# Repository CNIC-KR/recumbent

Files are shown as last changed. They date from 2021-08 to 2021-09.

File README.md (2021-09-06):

# 방치자전거 부품으로 3륜 리컴번트 만들기

YouTube 비디오 링크:  

IMAGE ALT TEXT HERE (https://www.youtube.com/watch?v=EfHd-qzypDQ)

___
본 자전거는 미국 DIY 창작자 Atomic Zombie 의 Streetfox Tadpole Trike 설계를 기반으로 제작되었습니다.  
제작 도면은 Atomic Zombie의 웹사이트에서 직접 구입하셔야 합니다.  
[https://www.atomiczombie.com/streetfox-tadpole-trike-diy-plan/](https://www.atomiczombie.com/streetfox-tadpole-trike-diy-plan/)  
___
**주의**

충남사회혁신센터는 공유된 리컴번트 자전거 설계의 안전성, 신뢰성, 내구성, 기능을 보장하지 않습니다. 또한 공유된 자전거 설계를 통해 제작된 어떠한 장치의 안성,신뢰성, 내구성, 기능에 대해서도 책임을 지지 않습니다. 공유된 설계에 기반해 장치를 제작하는 것은 전적으로 제작자의 재량에 의한 것이며 충남사회혁신센터는 공유된 정보를 활용해 내려진 결정이나 행동에 대해서 법적인 책임이 없습니다. 

**안전** 

본 제작 가이드에서 사용하는 공구들은 적절한 안전장비를 갖추지 않고 작업할 경우 제작자에게 상해를 입힐 수 있습니다. 특히 용접의 경우 전문적인 교육을 이수하는 것이 안전한 작업을 위해 바람직합니다. 작업시 보안경, 용접장갑, 용접마스크, 귀마개 등을 갖추고 안전하게 작업하세요! 
___

**•0_리컴번트 제작 가이드:**  
제작을 진행하신 김성수님의 제작 팁이 적혀있는 한국어 가이드입니다.  
https://forms.gle/e7z2dzJB1erC4kB48 에서 면책특약에 동의하신 후 다운받으실 수 있습니다.  
도면과 실제 제작이 다른 부분이 있으시 재료 구입전 **꼭** 읽어보셔야 합니다. 

**•1_리컴번트 부품 목록:**  
제작에 필요한 재료들의 수량과 구입처가 적혀있습니다.  

**•2_용접지그 도면:**  
프레임 용접에 필요한 용접지그의 2D 도면입니다.  
구조를 파악하기 위한 3D 파일은 아래 링크에서 확인하실 수 있습니다.  

**•용접지그 3D 파일:**  
https://cad.onshape.com/documents/e19db32aaa2f906931428a36/w/65d13d293f960f246c17134b/e/6adec4346e6a5c44e0e556bb

**•3_헤드튜브 바이스 도면/4_헤트튜브 바이스 하부 도면:**  
지그에서 헤드튜브 고정에 사용되는 바이스 상•하부의 도면입니다. 각파이프를 가공하여 제작합니다.  

**•5_tube_notcher_AngleCalculation.f3d :**  
헤드 튜브와 암 프레임이 만나는 각도를 표시한 선으로만 이루어진 CAD 도면입니다. 제작가이드 4.리컴번트 제작 부분을 참고하세요.  
 f3d 확장자는 Autodesk Fusion 360으로 열람하셔야합니다.  
 DWG파일과 캡쳐이미지를 첨부하였습니다.  

**•6_tube_notcher_spacer.f3d:**  
원형파이프 노칭기에 40mm x 40mm사각파이프를 물려서 가공할 수 있는 어답터입니다. 3D 프린트하여 사용하셔야 합니다. STL 파일과 캡쳐이미지를 첨부했습니다.

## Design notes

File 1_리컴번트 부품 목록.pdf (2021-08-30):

지그용 부품 | 항목 | 규격 | 갯수
알루미늄 프로파일 40x80mm | 600mm | 2 | http://www.profileok.com/shop/item.php?it_id=1400000012
알루미늄 프로파일 40x80mm | 1000mm | 1
알루미늄 프로파일 40x80mm | 920mm | 1
알루미늄 프로파일 40x80mm | 350mm | 2 본 부재의 길이를 늘려서 서서 작업 할 수 있도록 할 수 있다.
알루미늄 프로파일 40x80mm | 780mm | 1 납품한 지그와 다른 부분으로써 바퀴를 끼웠을때 걸리는 것을 피하고자 팔의 길이를 줄였다.
알루미늄 프로파일 40x80mm | 300mm | 2
알루미늄 프로파일 40x80mm | 200mm | 2
80면용 앵글 | 75x75 | 8 | http://www.profileok.com/shop/item.php?it_id=1500000008
40면용 앵글 | 80x37 | 6 | http://www.profileok.com/shop/item.php?it_id=1500000006
80면용 앵글 | 75x40 | 1 | http://www.profileok.com/shop/item.php?it_id=1500000004
샘스렌치볼트 | M8 25 | 100
스프링 너트 | M8 | 100
조절좌 | A-VP 12-90 | 4 | http://www.profileok.com/shop/item.php?it_id=1700000002
풋베이스 | DAFB4080(M12) | 4 조절좌를 달기 위한 판 | http://www.profileok.com/shop/item.php?it_id=1500000051
M8x25 렌치볼트 | 16 풋베이스를 프로파일에 연결하기 위한 볼트
플라스틱 앤드캡 | DEC4080 | 10 | http://www.profileok.com/shop/item.php?it_id=1500000039
클램프 레버 | M8x30 | 4 | https://www.coupang.com/vp/products/1504455925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
클램프 레버 | M8x50 | 2 | https://www.coupang.com/vp/products/1504455925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
노브 | M8x50 | 4 | https://www.coupang.com/vp/products/1495893683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
볼반 바이스 | 2 | https://www.coupang.com/vp/products/2053120294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
m10 와샤 | 20
튜브 노칭기 | 파이프노칭기 파이프홀가공 PNM1-1.2 PIPE | 1 | https://www.coupang.com/vp/products/191613037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
모터 | 바팡 750w 키트 | 바이크샵에게만 판매하기 때문에 전화해서 사장님께 허락을 받아야 한다. | https://bafangs.com/?page_id=68
스피드 센서 케이블 연장선 | 1 | https://www.aliexpress.com/item/32985406351.html?spm=a2g0s.9042311.0.0.44024c4dlOSSRs
쓰로틀 케이블 연장선 | 1 | https://www.aliexpress.com/item/1005001593406432.html?spm=a2g0s.9042311.0.0.44024c4dlOSSRs
xt60 커넥터 | 암수 | 2 | https://www.coupang.com/vp/products/5579805640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
실리콘 피복케이블 _레드 | AWG 16 | 2m | https://www.coupang.com/vp/products/4938811079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
실리콘 피복케이블 _블랙 | AWG 16 | 2m | https://www.coupang.com/vp/products/4938811079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
브레이크 | 브레이크 레버 | 앞바퀴용 더블 케이블 레버 | 납품한 자전거에는 설치 되어 있지 않음, 구매한 것이 나중에 배송왔으나 엉뚱한 트리플케이블용이https://www.aliexpress.com/item/4000481092339.html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
디스크 브레이크 | 드럼 브레이크를 쓰는 자전거를 부품으로 쓸 때 교체 가능 | https://www.aliexpress.com/item/33003381582.html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
디스크 브레이크 캘리퍼 브라켓 | 드럼 브레이크를 쓰는 자전거를 부품으로 쓸 때 교체 가능 | https://www.aliexpress.com/item/1005001273485667.html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
디스크 브레이크 캘리퍼 브라켓 | 새로 찾은 것 _ 드럼 브레이크를 쓰는 자전거를 부품으로 쓸 때 교체 가능 | https://www.aliexpress.com/item/1005002362649962.html?spm=a2g0s.8937460.0.0.478f2e0ea6u5FI
디스크 브레이크 디스크 어댑터 | 드럼 브레이크를 쓰는 자전거를 부품으로 쓸 때 교체 가능 | https://www.aliexpress.com/item/32804783028.html?spm=a2g0s.9042311.0.0.2af14c4dVobYa1
브레이크 속선 | 250cm | 1 뒷브레이크 | https://www.coupang.com/vp/products/242433115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
브레이크 속선 | 178cm | 1 왼쪽 브레이크 | https://www.coupang.com/vp/products/242433115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
브레이크 속선 | 128cm | 1 오른쪽 브레이크 | https://www.coupang.com/vp/products/242433115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
브레이크 겉선 | 220cm | 2 뒷브레이크, 변속기 | https://www.coupang.com/vp/products/242433115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
브레이크 겉선 | 110cm | 1 왼쪽 브레이크 | https://www.coupang.com/vp/products/242433115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
브레이크 겉선 | 155cm | 1 오른쪽 브레이크 | https://www.coupang.com/vp/products/242433115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
브레이크 속선 마감재 | https://www.coupang.com/vp/products/242433115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
브레이크 겉선 마감재 | https://www.coupang.com/vp/products/242433115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
브레이크 패드 | https://www.coupang.com/vp/products/242433115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
기어속선 | 210cm | https://www.coupang.com/vp/products/242433115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
체인 | https://www.coupang.com/vp/products/285855464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
앞바퀴 | BMX용 20인치 휠 | 축 직경 14mm Axle | 2 | 아마존 이베이에서 엄청 뒤져서 샀었음.
조향 | 로드엔드 베어링 | M8 수나사형 왼나사 | 1 | 오프라인
로드엔드 베어링 | M8 수나사형 오른나사 | 1 | 오프라인
왼나사 (좌산) 너트 | M8 | 1 | https://www.coupang.com/vp/products/201407298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
오른나사 너트 | M8 | 1 | https://www.coupang.com/vp/products/201407298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
타이어 20인치 | 3 | https://www.coupang.com/vp/products/206663529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
튜브 | 3 | https://www.coupang.com/vp/products/206663529?itemId=610450948&vendorItemId=4601574894&isAddedCart=
림테이프 | 3 | https://www.coupang.com/vp/products/216521075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
홀쏘 | 34mm | 1 구한 자전거의 헤드 튜브 직경을 재보고 맞는 것을 구매
35mm | 1 구한 자전거의 시트 튜브 직경을 재보고 구매 | https://www.coupang.com/vp/products/1672860795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
바디
철재 각파이프 | 40x40mm 1.4t | 6m | 최소 판매단위가 6m | 오프라인
철재 각파이프 | 20x20mm 1.4t | 6m | 최소 판매단위가 6m | 오프라인
철판 | 4t
철편 | 100x30mm 10t

### 자전거 공구 세트

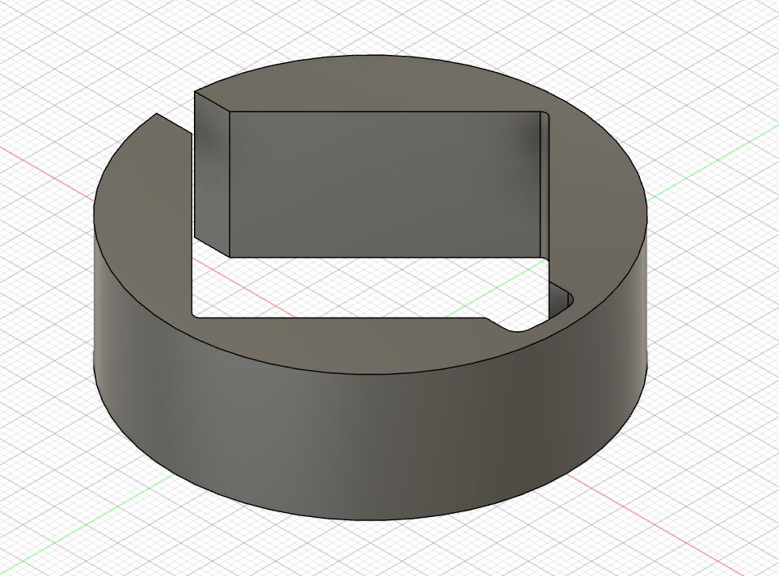
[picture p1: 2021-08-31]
6_tube_notcher_spacer(JPG).JPG

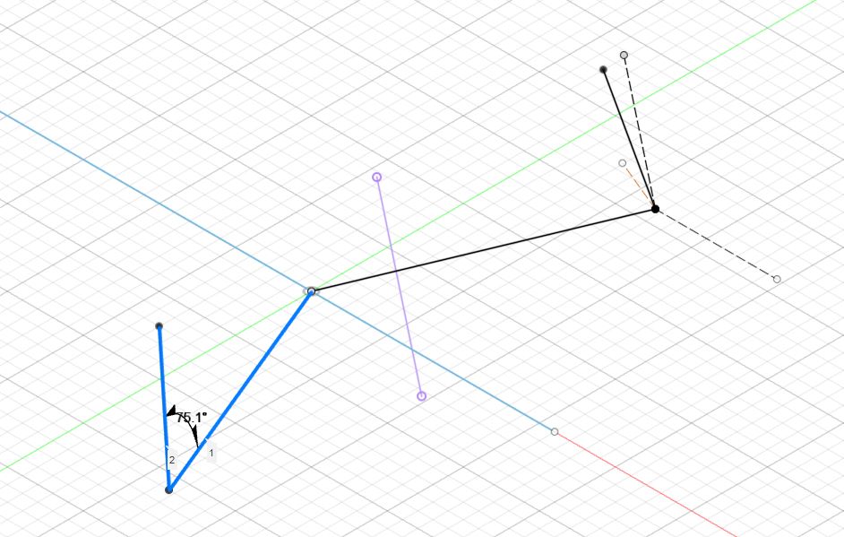
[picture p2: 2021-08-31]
5_tube_notcher_AngleCalculation(JPG).JPG

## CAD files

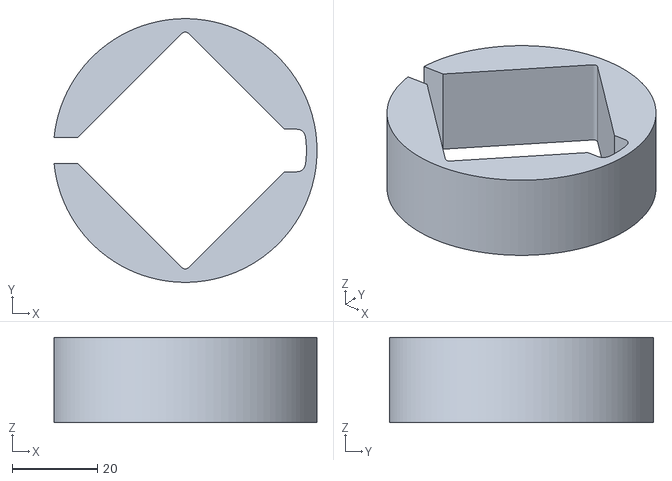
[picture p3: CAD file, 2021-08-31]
6_tube_notcher_spacer(STL).stl
61.8 x 62.0 x 20.0

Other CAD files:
5_tube_notcher_AngleCalculation(DWG).dwg
5_tube_notcher_AngleCalculation.f3d
6_tube_notcher_spacer.f3d

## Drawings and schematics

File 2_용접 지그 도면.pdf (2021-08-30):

2
1

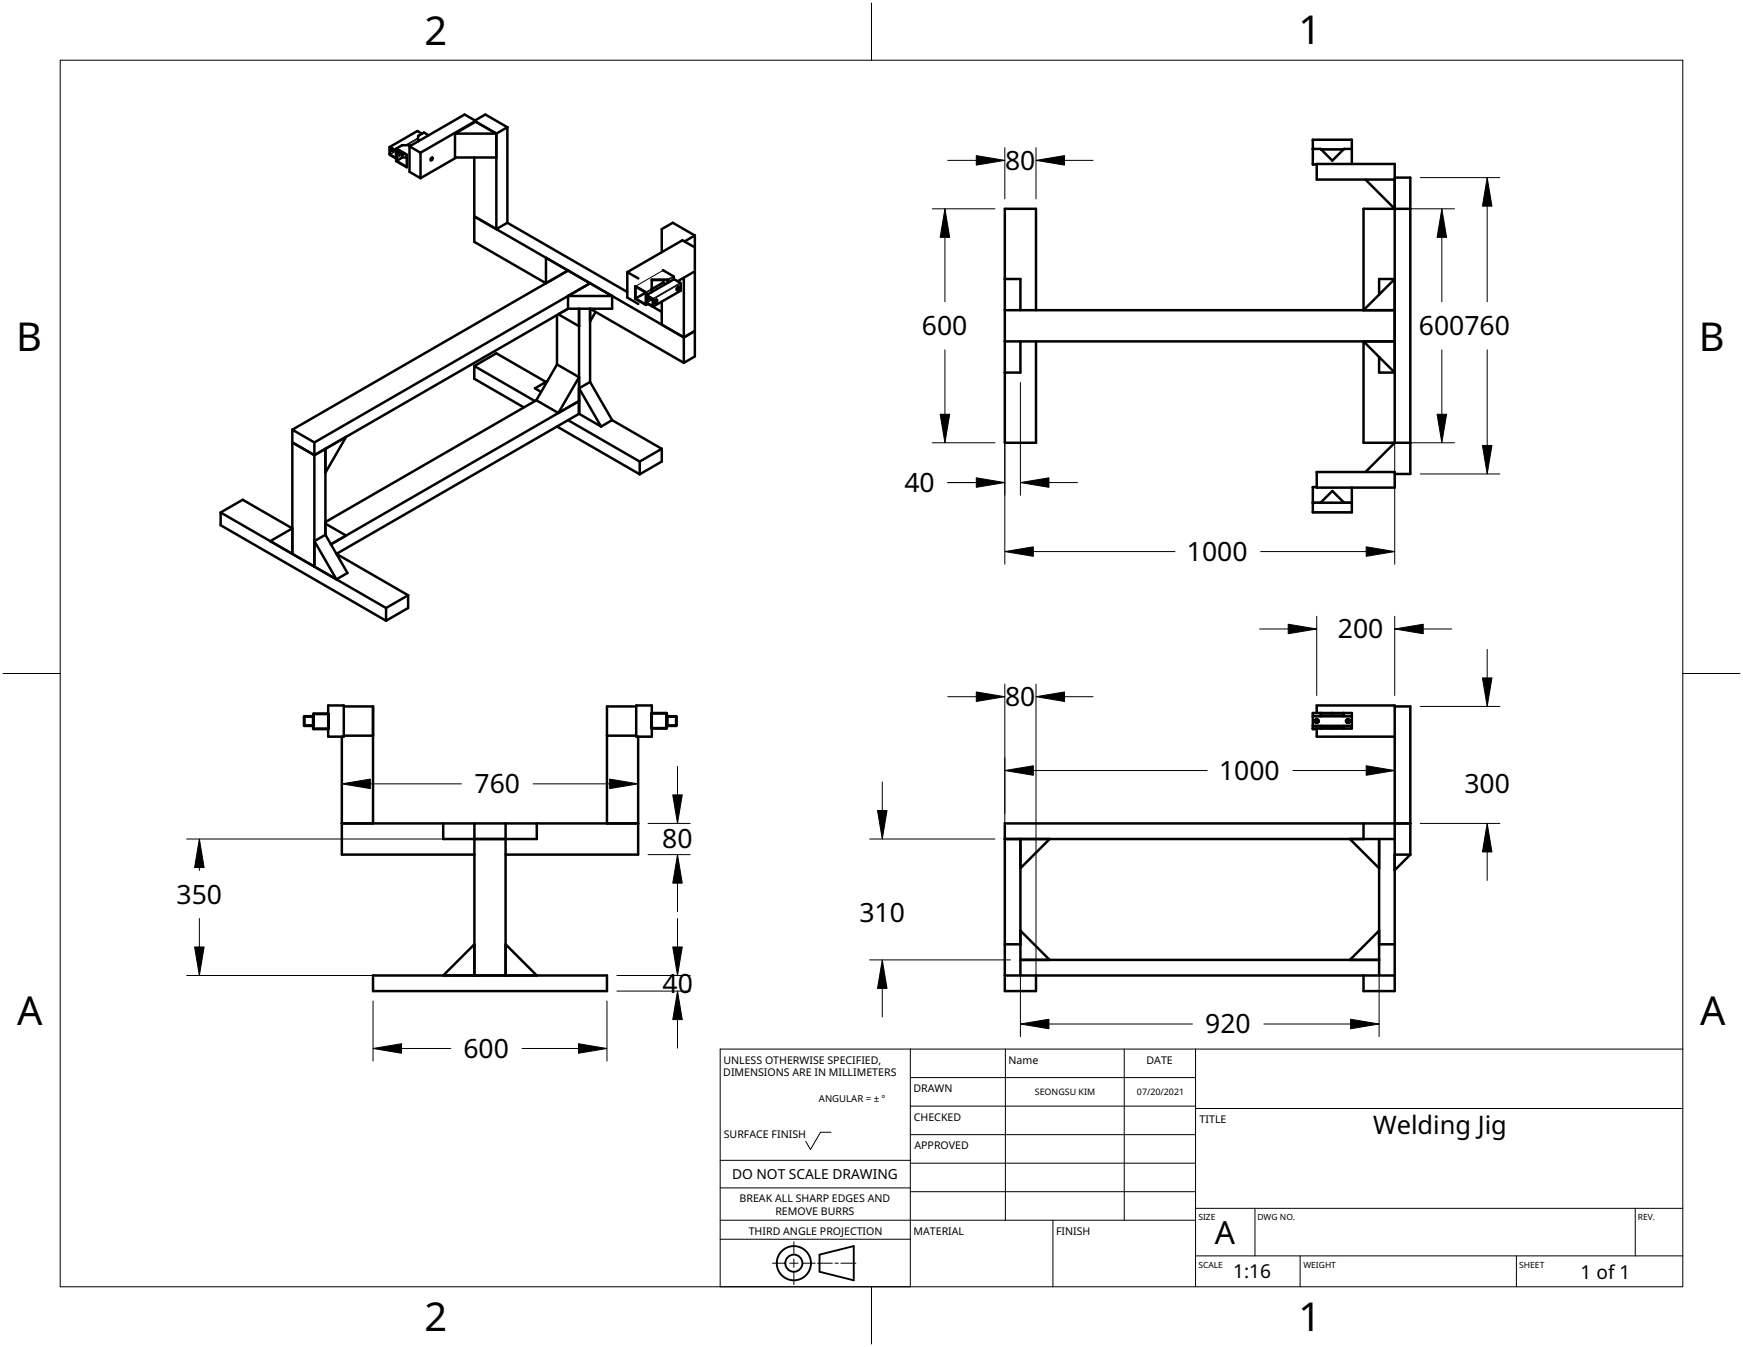
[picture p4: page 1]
MATERIAL; FINISH

UNLESS OTHERWISE SPECIFIED, DIMENSIONS ARE IN MILLIMETERS ANGULAR = ± ° SURFACE FINISH | | Name | DATE

DRAWN | SEONGSU KIM | 07/20/2021

CHECKED | | | TITLE Welding Jig

APPROVED

DO NOT SCALE DRAWING

BREAK ALL SHARP EDGES AND

REMOVE BURRS
THIRD ANGLE PROJECTION

SIZE A | DWG NO. | REV.

SCALE 1:16 | WEIGHT | SHEET 1 of 1

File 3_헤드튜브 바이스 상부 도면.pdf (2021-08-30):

2
1

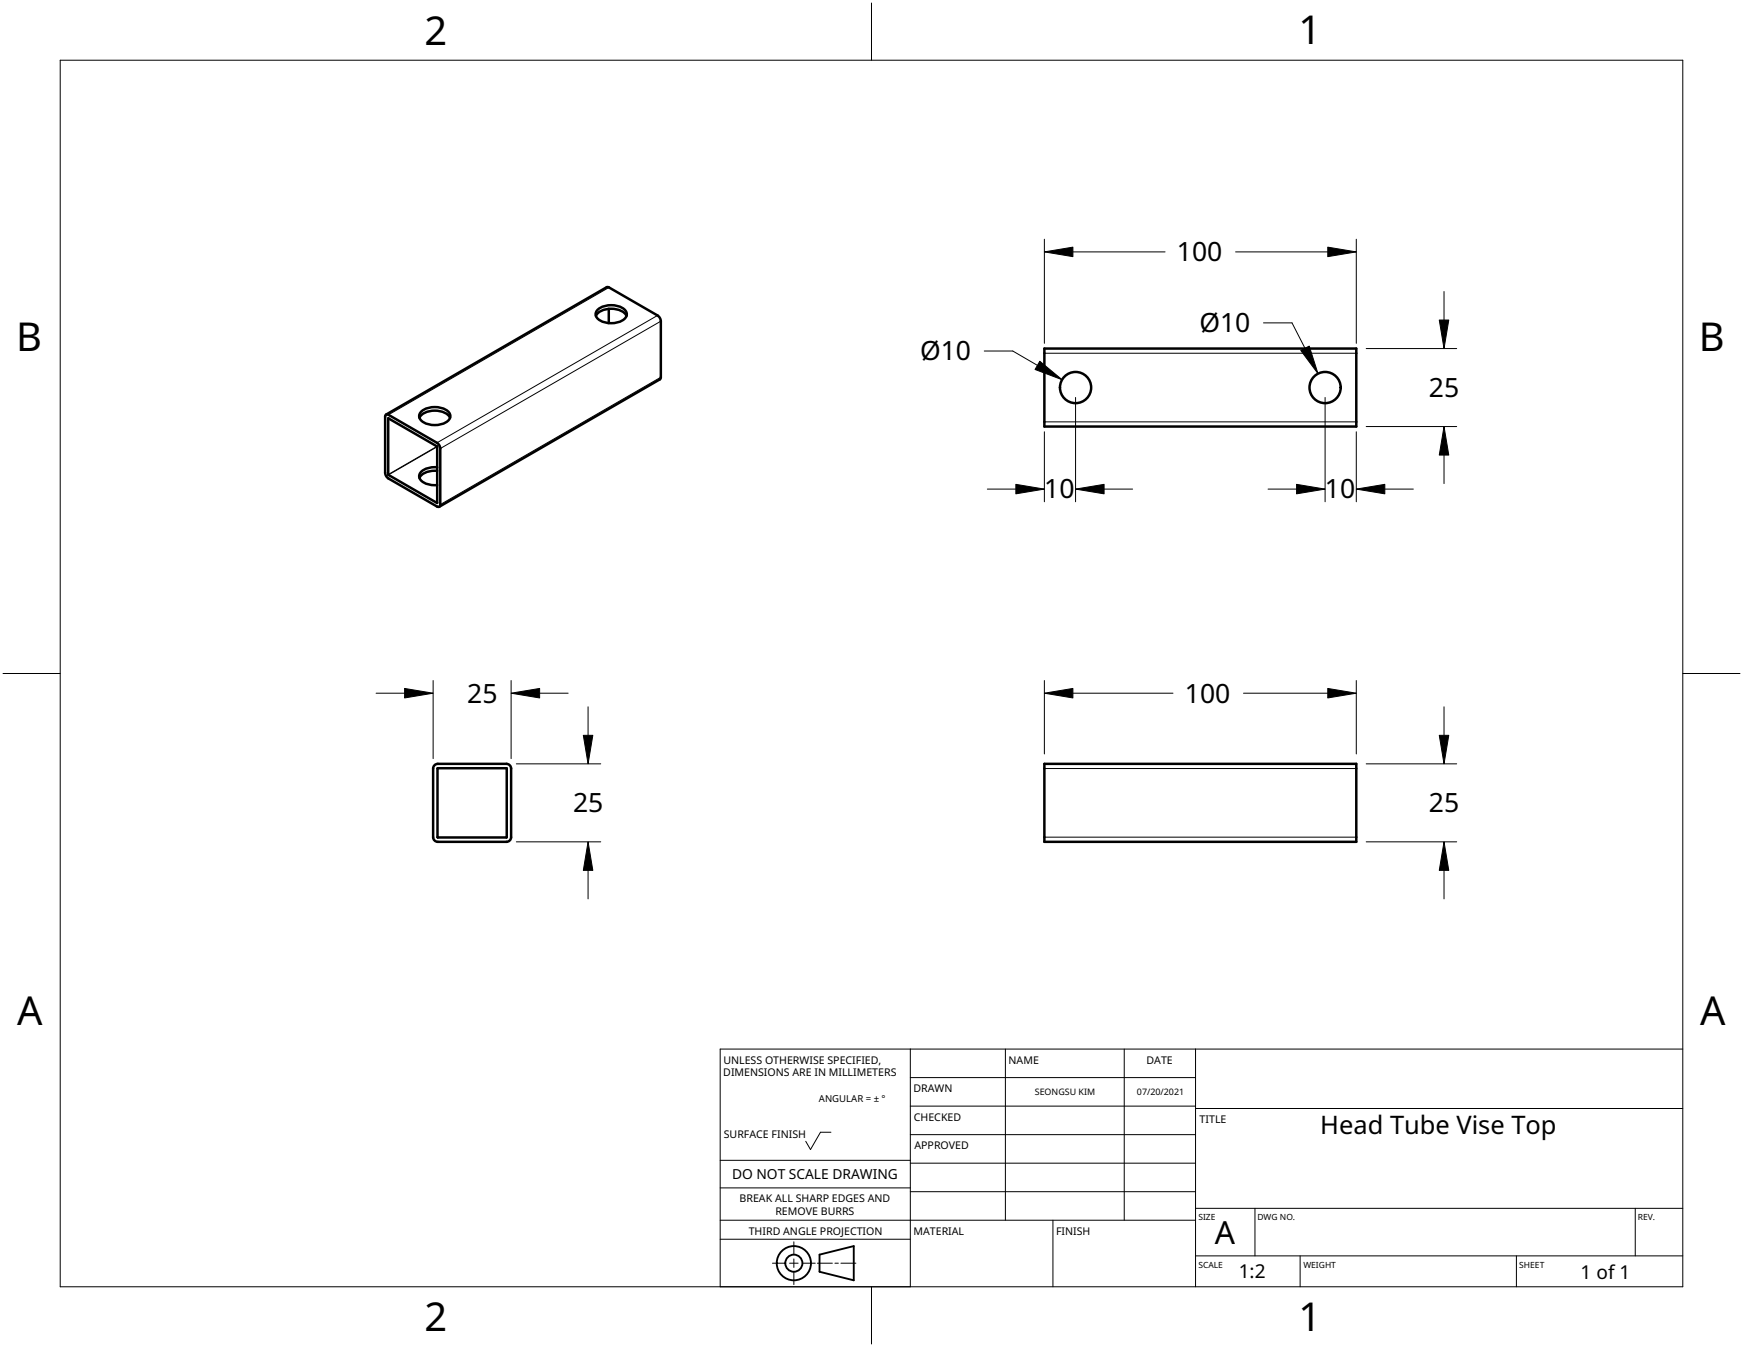
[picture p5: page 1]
MATERIAL; FINISH

UNLESS OTHERWISE SPECIFIED, DIMENSIONS ARE IN MILLIMETERS ANGULAR = ± ° SURFACE FINISH | | NAME | DATE

DRAWN | SEONGSU KIM | 07/20/2021

CHECKED | | | TITLE Head Tube Vise Top

APPROVED

DO NOT SCALE DRAWING

BREAK ALL SHARP EDGES AND

REMOVE BURRS
THIRD ANGLE PROJECTION

SIZE A | DWG NO. | REV.

SCALE 1:2 | WEIGHT | SHEET 1 of 1

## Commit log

2021-08-31 파일 번호 추가
    [5_tube_notcher_AngleCalculation(DWG).dwg, 5_tube_notcher_AngleCalculation.f3d, 6_tube_notcher_spacer(STL).stl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]
2021-09-05 Delete 0_리컴번트 제작 가이드.pdf
    제작가이드 링크 업데이트
